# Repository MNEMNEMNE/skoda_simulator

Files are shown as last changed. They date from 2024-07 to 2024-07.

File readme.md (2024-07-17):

# Skoda simulator - demo

Functional demonstrator of simulator for driving school based on Skoda 120 cabin.

Hardware is based on the original mechanic control mechanism, which drives the projecting round board. The whole control center is replaced by the new hardware. 
Original servo motor is too weak to reliable drive the steering mechanism. The servo motor position sensor was needed to get reliable the motor position.
In the demonstrator is the servo motor still populated, but unconnected. The output axis of the servo motor is directly connected to the stepping motor.
The servo position sensor is removed and the space is covered by the servo motoor position sensor cup, which simultaneously holds the new electronic.

The new electonic is connected to:  
 - DC motor controlling the forward drive
 - stepping motor controlling the steering mechanism 
 - getting the signals from the phototransisotrs collecting the information from off-road ride
 
 ### Part list
 
 - stepping motor **36H12HM**
 - stepping motor holder
 - stepping motor axis connect
 - servo motor position cup
 - Arduino nano
 - A4988 stepping motor module (current set to 0,33A)
 - mini 360 DC/DC buck
 
 ### Files:
 
`demo/demo.ino` software for the Arduino Nano board  
`schema.sch` schematic in eagle  
`redukce_motoru_simulator_autoskoly.f3d` 3D models for the 3D printed parts    
`stl/*.stl` stl files for 3d printed parts

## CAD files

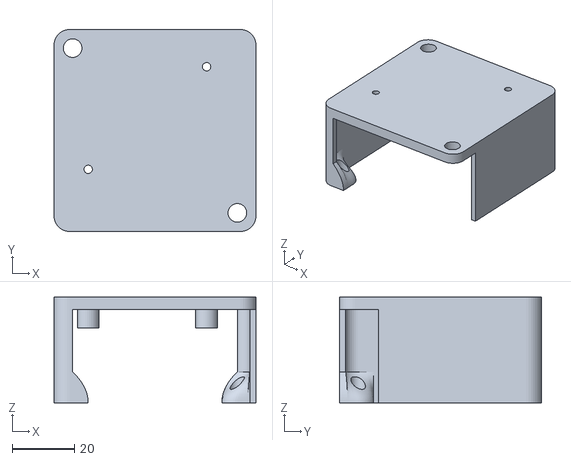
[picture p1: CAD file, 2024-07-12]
stl/electronic holder.stl
65.0 x 65.0 x 34.0

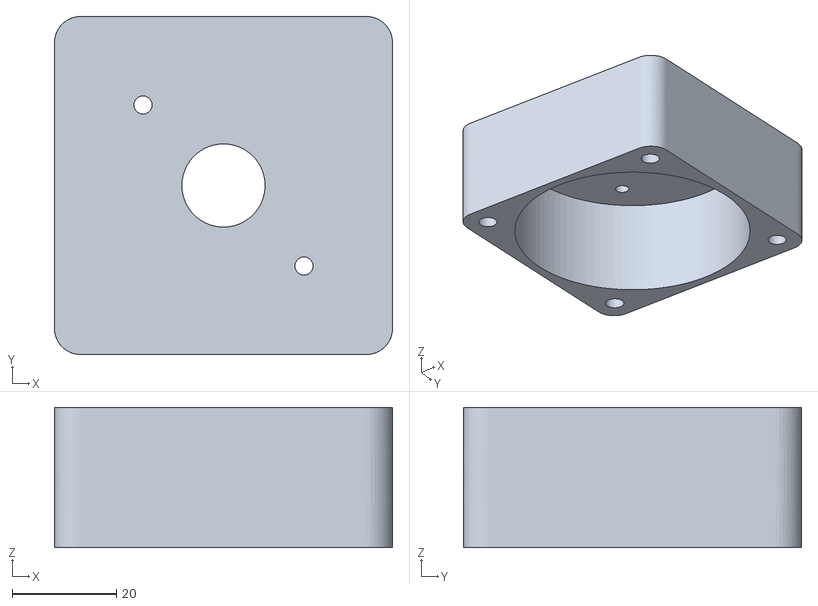
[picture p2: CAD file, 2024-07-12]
stl/stepper motor mount.stl
65.0 x 65.0 x 27.0

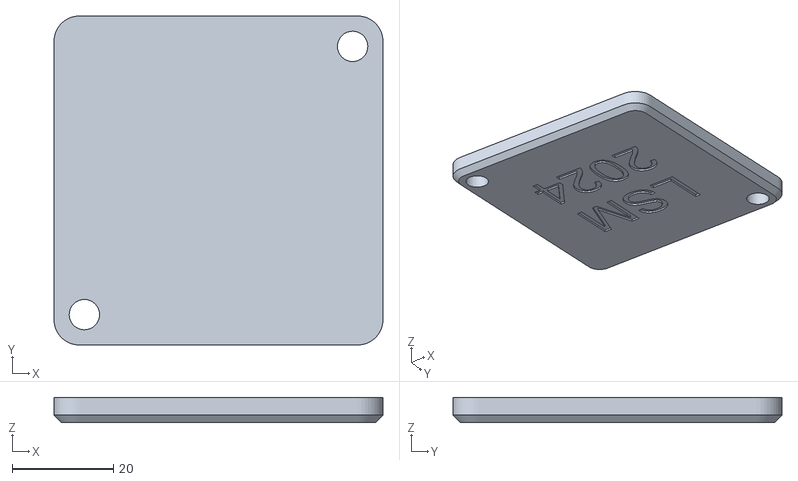
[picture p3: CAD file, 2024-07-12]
stl/electronic cover.stl
65.0 x 65.0 x 5.00

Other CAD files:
redukce_motoru_simulator_autoskoly.f3d

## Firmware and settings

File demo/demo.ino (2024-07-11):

// pin definition
#define FORWARD_MOTOR 10  // PWM output pin for motor forward

#define FORWARD_ONROAD_SPEED    200 // Speed of forward drive motor during drive on road 
#define FORWARD_OFFROAD_SPEED   50  // Speed of forward drive motor during off-road drive

#define OFFROAD_LEFT  A1   // Input pin for the phototransistor signaling left side off-road drive
#define OFFROAD_RIGHT A2   // Input pin for the phototransistor signaling right side off-road drive

#define OFFROAD_LEVEL 128  // Values of the off-road analog inputs below this value
                           // signal the off-road drive

// stepping motor pin definition
#define STEERING_ENABLE_N_PIN   2
#define STEERING_DIR_PIN        7
#define STEERING_STEP_PIN       6
#define STEERING_MS1_PIN        3
#define STEERING_MS2_PIN        4
#define STEERING_MS3_PIN        5
// stepping motor parameters
#define STEERING_STEPS          400 // step count for whole rotation
#define STEERING_MICROSTEPS     1
#define STEERING_RPM            120 // rotate speed of the steering motor during the steering movement

#define STEERING_STEPS          400          

#include <A4988.h>

A4988 steer(STEERING_STEPS, STEERING_DIR_PIN, STEERING_STEP_PIN, STEERING_ENABLE_N_PIN, STEERING_MS1_PIN, STEERING_MS2_PIN, STEERING_MS3_PIN);

void setup() {

  Serial.begin(115200);
  Serial.println("");
  Serial.println("Skoda driving school demonstrator made in LSM Stepanov 2024.");

  // pin initialize
  pinMode(LED_BUILTIN, OUTPUT);
 
  pinMode(FORWARD_MOTOR, OUTPUT);

  pinMode(OFFROAD_LEFT, INPUT);
  pinMode(OFFROAD_RIGHT, INPUT);

  steer.setEnableActiveState(LOW);
  steer.begin(STEERING_RPM, 2);
}

int getTargetSteerPosition(bool offroadLeft, bool offroadRight)
{
  if(!offroadLeft && !offroadRight)
  {
    // drive on road

    // drive forward full speed and straight
    analogWrite(FORWARD_MOTOR, FORWARD_ONROAD_SPEED);
    return 0;
  }
  
  // drive offroad
  
  // slow down the forward speed
  analogWrite(FORWARD_MOTOR, FORWARD_OFFROAD_SPEED);
  
  if(offroadLeft && !offroadRight)
  {
    // away of road to the left side - go to the right
    return STEERING_STEPS;
  }
  else if (!offroadLeft && offroadRight)
  {
    // away of road to the right side - go to the left
    return -STEERING_STEPS;
  }
  // completely away of the road - go straight
  return 0;
}

// the loop function runs over and over again forever
void loop() {

  static bool offroadLeft = false,
              offroadRight = false;
  static int targetSteerStepPosition = 0;

  // get new states
  bool newOffroadLeft = analogRead(OFFROAD_LEFT) < OFFROAD_LEVEL;
  bool newOffroadRight = analogRead(OFFROAD_RIGHT) < OFFROAD_LEVEL; 

  if ( (offroadLeft != newOffroadLeft) || (offroadRight != newOffroadRight) )
  {
    // road state changed

    // print states
    Serial.print("Left:");
    Serial.print(newOffroadLeft ? "offroad" : "onroad");
    Serial.print(", Right:");
    Serial.println(newOffroadRight ? "offroad" : "onroad");

    int newTargetSteerStepPosition = getTargetSteerPosition(newOffroadLeft, newOffroadRight);

    // set the stepper to go to the newTargetSteerStepPosition

    int currentStepPosition = targetSteerStepPosition - steer.getStepsRemaining();

    steer.startMove(newTargetSteerStepPosition - currentStepPosition);

    targetSteerStepPosition = newTargetSteerStepPosition;
  }
  
  // update states
  offroadLeft = newOffroadLeft;
  offroadRight = newOffroadRight; 

  // proceed the steer stepper motor task
  steer.nextAction();
}

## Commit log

2024-07-07 Add off-road sensors
2024-07-09 add first early version of the arduino project
2024-07-11 first testing release
    [redukce_motoru_simulator_autoskoly.f3d]
2024-07-11 style: remove code for old driver
2024-07-11 feat: refactor
    take out the code for getting the next steer position to its own function, while fixing some and making the states boolean update
    [demo.ino]
2024-07-12 Add stl files
    [electronic cover.stl, electronic holder.stl, stepper motor mount.stl]
